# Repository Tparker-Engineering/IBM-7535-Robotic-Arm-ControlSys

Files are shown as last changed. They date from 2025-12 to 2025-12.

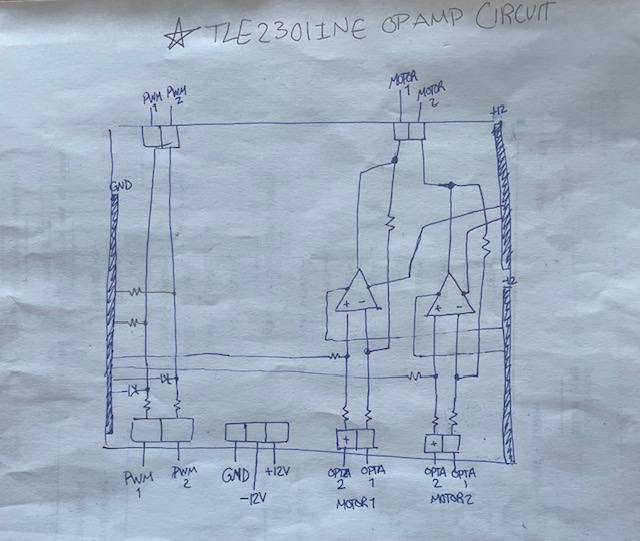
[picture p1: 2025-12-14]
Datasheets_Wiring/OpAmpCircuit.jpg

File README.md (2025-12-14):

# IBM-7535-Robotic-Arm-ControlSys

Watch the demo video (https://youtu.be/oRWTlzxxvLM)

## Project Overview
**Rewired & ReARMed** is a senior design project focused on retrofitting an **IBM 7535 SCARA robot** from the 1980s with modern control hardware and software.  
The goal was to replace the obsolete control system with an **Arduino Opta PLC** while maintaining the robot’s functionality and old legacy systems.

Originally designed for industrial automation, the IBM 7535 had been rendered non-functional due to outdated electronics, limited documentation, and component issues. Our team reverse-engineered the system, traceed its wiring diagrams, and designed a new control approach compatible with the existing **Yaskawa Servopak motor drivers**. This included:
- developing an **analog ±10V control solution** using op-amp subtractor circuits, enabling bidirectional motor control from the Arduino Opta’s 0–10V outputs
- making a **voltage divider circuit using Zener diodes** to enable bidirectional control for the stepper motor
- successfully pulse the stepper motor at operable speed
- send voltage to operate the solenoids

In addition to wiring the OPTA to the system, we programmed control logic within the Arduino IDE, verified the sensors, and ensured the motors responded accurately to control inputs. The result was a functioning robot capable of smooth and controlled movement, demonstrated successfully in a live test.
While the SCARA is operable and functionable, it still needs future work, like finishing the encoders and tracing a possible overcurrent issue in the servopacks, an issue that is correlated to the motor drift.
Despite the small issues, the team was able to pave a way for future teams to work on the 7535 SCARA and hopes to see the robotic arm be completely restored and retrofitted with the versatility and capability of modern technology.

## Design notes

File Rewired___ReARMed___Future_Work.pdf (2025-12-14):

# Rewired & ReARMed - Future Work

AnMinh Vuong | Rachel Garcia | Travis Parker
Xander Addington | Angelina Abuhilal
| July 2025

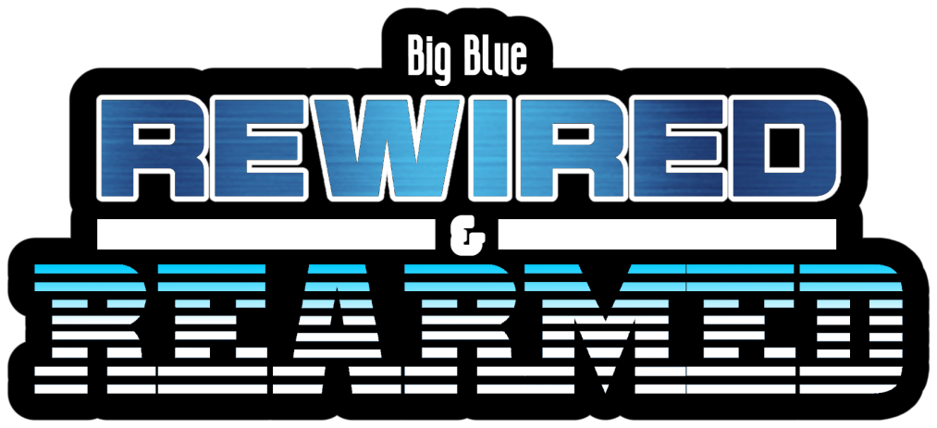
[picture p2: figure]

1

## Introduction

This document is meant for the next team who ends up with the robot. We wanted to be able to share our thoughts and concerns with the project in the future.

## System Startup Notes

- For any test or demo code, position the Theta1 arm slightly clockwise of the home sensor before startup. The Theta2 arm should also be slightly clockwise of the home sensor; the robot will drift counterclockwise into the sensor during initialization.

## Encoder and Sensor Wiring

- Encoders on WD12A are wired to pins 3, 1, and 5. Future teams may need to supply +12 V to pin 19 and GND to pins 2, 4, and 6 (to be verified).
- On WD13A, encoders are wired to pins 7, 9, and 11.
- For Theta1 and Z-axis gripper sensors, a temporary software pull hack was used; a proper pull resistor circuit is recommended.
- Stepper motor sensors (R+ Area and Rhome) on WD08B are currently non-functional; further troubleshooting is required.

## Safety Recommendations

- Implement an emergency shut-off switch between TB1R and ground; TB1R to ground enables power to the manipulator.
- Improve initialization routines and safety logic in software.

## Circuit Limitations and Recommendations

- Current op-amp circuit is limited to 5 V output. Avoid exceeding this due to unknown servo potentiometer settings.
- Recommend creating a proper PCB instead of continuing with prototype boards.

2

## Wiring and Connectors

- Existing wiring with Deutsch connectors was reused. Spare Deutsch pins are provided for future wiring.
- If possible, design improved wiring harnesses and connectors.

## Servo and Encoder Issues

- Encoders may be causing servo drift in Theta1 and Theta2 due to undervoltage (red servo light indicator).
- If encoder fixes do not stop red lights, investigate possible overcurrent, undercurrent, overvoltage, or undervoltage conditions.

## Removed Legacy Hardware

- Removed MTCB, CPU, and FEC boards. The relay board can be removed, but TB1R is attached to it.

## Future Software Goals

- Optical encoders should enable precise position control (e.g., Theta1 = 61, Theta2 = 120 should move directly to that position).
- Develop a touchscreen GUI tablet similar to the original (now obsolete) controller.

## Priorities for Future Teams

Computer Engineering:

1. Get encoders working.
2. Get stepper limit sensors working.
3. Install emergency shut-off switch.
4. Improve circuit design and wiring.
5. Mount Arduino Opta units to DIN rail and robot.

Secondary:
- Troubleshoot servos if encoder fixes fail.

Computer Science and Software:

1. Develop GUI.
2. Assist CpE team with encoder position grid/matrix.

3

## Contacts

AnMinh Vuong
Discord - Zetsubou999
Email - anminh0102@gmail.com

Travis Parker
Discord - dvrkstar

Angie Abuhilal
Discord - farfarahah

Xander Addington
Discord - xer0727

Rachel Garcia
Discord - rig3121

4

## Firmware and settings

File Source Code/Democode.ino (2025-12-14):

#include "OptaBlue.h"

/*Theta1 needs to be slight off home cam roller. Theta2 needs to be slightly off home sensor. Stepper belt needs to be in a safe postion. 
Close air compressor valve on bottom of aircompressor and plug in compressor. PSI for robot is 80PSI do not exceed.
Demo will execute a simulation of pick and place operation.*/

// Relay outputs
#define Z_DOWN_RELAY    0  // RELAY1 (D0)
#define GRIPPER_RELAY   1  // RELAY2 (D1)

// Sensor inputs (core Opta GPIO)
#define Z_UP_PIN        A6  // Z-UP sensor input
#define Z_DOWN_PIN      A2  // Z-DOWN sensor input

bool gripperCycleDone = false;

enum Theta1State {
  THETA1_IDLE,
  THETA1_MOVE_CCW_1,
  THETA1_HOLD_1,
  THETA1_MOVE_CCW_2,
  THETA1_HOLD_2,
  THETA1_TO_OVERRUN,
  THETA1_TO_HOME,
  THETA1_DONE
};

enum Theta2State {
  THETA2_IDLE,
  THETA2_MOVE_CCW_1,
  THETA2_HOLD_1,
  THETA2_MOVE_CCW_2,
  THETA2_HOLD_2,
  THETA2_TO_OVERRUN_POS,
  THETA2_TO_OVERRUN_NEG,
  THETA2_TO_HOME,
  THETA2_DONE
};

Theta1State theta1_state = THETA1_IDLE;
Theta2State theta2_state = THETA2_IDLE;

bool stepper_active = false;
uint32_t stepper_start_time = 0;
uint8_t stepper_channel = 0;


AnalogExpansion aexp;
float lastVoltages[7] = {0};

void safeSetVoltage(uint8_t channel, float voltage) {
  if (lastVoltages[channel] != voltage) {
    aexp.pinVoltage(channel, voltage);
    lastVoltages[channel] = voltage;
  }
}

void spinStepper(uint8_t channel) {
  aexp.setPwm(channel, 1600, 25);
  OptaController.update();
  delay(250);
  aexp.setPwm(channel, 1600, 0);
  OptaController.update();
}
/*
void runGripperSequence() {
  // Z-UP pull-up hack
  pinMode(Z_UP_PIN, OUTPUT); digitalWrite(Z_UP_PIN, HIGH); delay(1);
  pinMode(Z_UP_PIN, INPUT); delayMicroseconds(5);
  bool zUpActive = (digitalRead(Z_UP_PIN) == LOW);

  // === Software pull-up hack for Z-DOWN (A2) ===
  pinMode(Z_DOWN_PIN, OUTPUT);
  digitalWrite(Z_DOWN_PIN, HIGH);
  delay(1);
  pinMode(Z_DOWN_PIN, INPUT);
  delayMicroseconds(5);
  bool zDownActive = (digitalRead(Z_DOWN_PIN) == LOW);  // active-low

  digitalWrite(Z_DOWN_RELAY, HIGH);  // Lower Z
  delay(1000);
  digitalWrite(Z_DOWN_RELAY, LOW);  // Raise Z
  delay(200);

/*
  if (zUpActive) {
    digitalWrite(Z_DOWN_RELAY, HIGH);  // Lower Z
    delay(500);

    unsigned long startTime = millis();
    while ((millis() - startTime) < 5000) {
      // Z-DOWN pull-up hack
      pinMode(Z_DOWN_PIN, OUTPUT); digitalWrite(Z_DOWN_PIN, HIGH); delay(1);
      pinMode(Z_DOWN_PIN, INPUT); delayMicroseconds(5);
      bool zDownActive = (digitalRead(Z_DOWN_PIN) == LOW);

      if (zDownActive) {
        digitalWrite(GRIPPER_RELAY, HIGH);  // Grip
        delay(1000);
        digitalWrite(GRIPPER_RELAY, LOW);
        break;
      }
    }

    digitalWrite(Z_DOWN_RELAY, LOW);  // Raise Z
  }
  
  delay(200);
}
*/

// Timing parameters
const unsigned long theta1_moveDuration1 = 4000;
const unsigned long theta1_moveDuration2 = 2000;
const unsigned long theta1_holdDuration = 4000;
unsigned long theta1_timer = 0;

const unsigned long theta2_moveDuration1 = 1250;
const unsigned long theta2_moveDuration2 = 500;
const unsigned long theta2_holdDuration1 = 8000;
const unsigned long theta2_holdDuration2 = 4000;
unsigned long theta2_timer = 0;

void setup() {
  Serial.begin(115200);
  OptaController.begin();

  pinMode(A0, INPUT_PULLUP);  // θ₁ home
  pinMode(A1, INPUT_PULLUP);  // θ₁ overrun
  pinMode(A3, INPUT_PULLUP);  // θ₂ home
  pinMode(A4, INPUT_PULLUP);  // θ₂ overrun−
  pinMode(A5, INPUT_PULLUP);  // θ₂ overrun+
  // Set relay outputs
  pinMode(Z_DOWN_RELAY, OUTPUT);
  pinMode(GRIPPER_RELAY, OUTPUT);
  digitalWrite(Z_DOWN_RELAY, LOW);
  digitalWrite(GRIPPER_RELAY, LOW);


  while (OptaController.getExpansionNum() == 0) {
    Serial.println("Waiting for analog expansion...");
    OptaController.update();
  }

  aexp = OptaController.getExpansion(0);

  aexp.beginChannelAsDac(2, OA_VOLTAGE_DAC, true, false, OA_SLEW_RATE_0);  // θ₁ CW
  aexp.beginChannelAsDac(3, OA_VOLTAGE_DAC, true, false, OA_SLEW_RATE_0);  // θ₁ CCW
  aexp.beginChannelAsDac(5, OA_VOLTAGE_DAC, true, false, OA_SLEW_RATE_0);  // θ₂ CW
  aexp.beginChannelAsDac(6, OA_VOLTAGE_DAC, true, false, OA_SLEW_RATE_0);  // θ₂ CCW

  aexp.setPwm(OA_PWM_CH_0, 1600, 0);  // Stepper CCW idle
  aexp.setPwm(OA_PWM_CH_1, 1600, 0);  // Stepper CW idle

  safeSetVoltage(2, 0.0f);
  safeSetVoltage(3, 0.4f);
  safeSetVoltage(5, 0.0f);
  safeSetVoltage(6, 0.4f);

  OptaController.update();
  Serial.println("Setup complete.");
}

void loop() {

  // θ₁ sensor reads
  pinMode(A0, OUTPUT); digitalWrite(A0, HIGH); delayMicroseconds(10);
  pinMode(A0, INPUT); delayMicroseconds(5);
  bool theta1_home = (digitalRead(A0) == LOW);

  pinMode(A1, OUTPUT); digitalWrite(A1, HIGH); delayMicroseconds(10);
  pinMode(A1, INPUT); delayMicroseconds(5);
  bool theta1_overrun = (digitalRead(A1) == LOW);

  // θ₂ sensor reads
  bool theta2_home = (digitalRead(A3) == LOW);
  bool theta2_overrunNeg = (digitalRead(A4) == LOW);
  bool theta2_overrunPos = (digitalRead(A5) == LOW);

  bool zDownActive = (digitalRead(Z_DOWN_PIN) == LOW);  // active-low
  bool zUpActive = (digitalRead(Z_UP_PIN) == LOW);


  OptaController.update();

  // θ₁ State Machine
  switch (theta1_state) {
    case THETA1_IDLE:
      safeSetVoltage(2, 0.0f);
      safeSetVoltage(3, 0.4f);
      if (theta1_home) {
        theta1_timer = millis();
        Serial.println("θ₁ → MOVE_CCW_1");
        theta1_state = THETA1_MOVE_CCW_1;
      }
      break;

    case THETA1_MOVE_CCW_1:
      safeSetVoltage(2, 0.0f);
      safeSetVoltage(3, 4.5f);
      if (millis() - theta1_timer >= theta1_moveDuration1) {
        safeSetVoltage(3, 0.0f);
        theta1_timer = millis();
        Serial.println("θ₁ → HOLD_1");
        theta1_state = THETA1_HOLD_1;
      }
      break;

    case THETA1_HOLD_1:
      safeSetVoltage(2, 0.0f);
      safeSetVoltage(3, 0.4f);
        
        aexp.setPwm(OA_PWM_CH_0, 1600, 25);  // start CCW
        OptaController.update();
        delay(250);
        aexp.setPwm(OA_PWM_CH_0, 1600, 1);  // almost 0% duty
        OptaController.update();
        delay(2);                               // allow hardware to register
        aexp.setPwm(OA_PWM_CH_0, 1600, 0);  // now fully stop
        OptaController.update();
        //runGripperSequence();

        delay(400);
        // Z-UP pull-up hack
        pinMode(Z_UP_PIN, OUTPUT); digitalWrite(Z_UP_PIN, HIGH); delay(1);
        pinMode(Z_UP_PIN, INPUT); delayMicroseconds(5);

        // === Software pull-up hack for Z-DOWN (A2) ===
        pinMode(Z_DOWN_PIN, OUTPUT);
        digitalWrite(Z_DOWN_PIN, HIGH);
        delay(1);
        pinMode(Z_DOWN_PIN, INPUT);
        delayMicroseconds(5);


        digitalWrite(Z_DOWN_RELAY, HIGH);  // Lower Z
        delay(1000);
        digitalWrite(Z_DOWN_RELAY, LOW);  // Raise Z
        delay(1000);


        delay(4000);
      /*
      if (stepper_active && millis() - stepper_start_time <= 300) {
        aexp.setPwm(stepper_channel, 1600, 1);  // almost 0% duty
        delay(2);                               // allow hardware to register
        aexp.setPwm(stepper_channel, 1600, 0);  // now fully stop
        OptaController.update();                // apply to hardware
        OptaController.update();
        stepper_active = false;
      }
      
      //spinStepper(OA_PWM_CH_0);  // For CCW
      if (!stepper_active) {
        aexp.setPwm(OA_PWM_CH_0, 1600, 25);  // start CCW
        OptaController.update();
        stepper_channel = OA_PWM_CH_0;
        stepper_start_time = millis();
        stepper_active = true;
        Serial.println("θ₁: Spinning stepper CCW");
      }
      
      */
      // Serial.println("θ₁: Spinning stepper CCW");
      if (millis() - theta1_timer >= theta1_holdDuration) {
        theta1_timer = millis();
        Serial.println("θ₁ → MOVE_CCW_2");
        theta1_state = THETA1_MOVE_CCW_2;
      }
      break;

    case THETA1_MOVE_CCW_2:
      safeSetVoltage(2, 0.0f);
      safeSetVoltage(3, 4.5f);
      if (millis() - theta1_timer >= theta1_moveDuration2) {
        safeSetVoltage(3, 0.0f);
        theta1_timer = millis();
        Serial.println("θ₁ → HOLD_2");
        theta1_state = THETA1_HOLD_2;
      }
      break;

    case THETA1_HOLD_2:
      safeSetVoltage(2, 0.0f);
      safeSetVoltage(3, 0.4f);
      // spinStepper(OA_PWM_CH_1);  // For CW

      delay(400);
      // Z-UP pull-up hack
      if (!gripperCycleDone) {
        delay(400);

        // Pull-up hack for Z-UP
        pinMode(Z_UP_PIN, OUTPUT); digitalWrite(Z_UP_PIN, HIGH); delay(1);
        pinMode(Z_UP_PIN, INPUT); delayMicroseconds(5);

        // Pull-up hack for Z-DOWN
        pinMode(Z_DOWN_PIN, OUTPUT);
        digitalWrite(Z_DOWN_PIN, HIGH);
        delay(1);
        pinMode(Z_DOWN_PIN, INPUT);
        delayMicroseconds(5);

        Serial.println("Z lowering...");
        digitalWrite(Z_DOWN_RELAY, HIGH);
        delay(1000);
        Serial.println("Z raising...");
        digitalWrite(Z_DOWN_RELAY, LOW);
        delay(1000);

        gripperCycleDone = true;
      }


      //runGripperSequence();

        /*
        aexp.setPwm(OA_PWM_CH_1, 1600, 25);  // start CCW
        OptaController.update();
        delay(250);
        aexp.setPwm(OA_PWM_CH_1, 1600, 1);  // almost 0% duty
        OptaController.update();
        delay(2);                               // allow hardware to register
        aexp.setPwm(OA_PWM_CH_1, 1600, 0);  // now fully stop
        OptaController.update();
        */

      /*
      if (!stepper_active) {
        aexp.setPwm(OA_PWM_CH_1, 1600, 25);  // start CCW
        OptaController.update();
        stepper_channel = OA_PWM_CH_0;
        stepper_start_time = millis();
        stepper_active = true;
        Serial.println("θ₁: Spinning stepper CCW");
      }
      */

      if (millis() - theta1_timer >= theta1_holdDuration) {
        Serial.println("θ₁: Spinning stepper CW");
        Serial.println("θ₁ → TO_OVERRUN");
        safeSetVoltage(3, 4.5f);

        theta1_state = THETA1_TO_OVERRUN;
      }
      break;

    case THETA1_TO_OVERRUN:
      if (theta1_overrun) {
        Serial.println("θ₁ overrun detected. Returning home.");
        safeSetVoltage(2, 5.2f);
        safeSetVoltage(3, 0.0f);
        theta1_state = THETA1_TO_HOME;
      }
      break;

    case THETA1_TO_HOME:
      if (theta1_home) {
        Serial.println("θ₁ returned to home.");
        safeSetVoltage(2, 0.0f);
        safeSetVoltage(3, 0.0f);
        theta1_state = THETA1_DONE;
      }
      break;

    case THETA1_DONE:
      // No action
      break;
  }

  // θ₂ State Machine
  switch (theta2_state) {
    case THETA2_IDLE:
      safeSetVoltage(5, 0.0f);
      safeSetVoltage(6, 0.4f);
      if (theta2_home) {
        theta2_timer = millis();
        Serial.println("θ₂ → MOVE_CCW_1");
        theta2_state = THETA2_MOVE_CCW_1;
      }
      break;

    case THETA2_MOVE_CCW_1:
      safeSetVoltage(5, 0.0f);
      safeSetVoltage(6, 4.5f);
      if (millis() - theta2_timer >= theta2_moveDuration1) {
        safeSetVoltage(6, 0.0f);
        theta2_timer = millis();
        Serial.println("θ₂ → HOLD_1");
        theta2_state = THETA2_HOLD_1;
      }
      break;

    case THETA2_HOLD_1:
      safeSetVoltage(5, 0.0f);
      safeSetVoltage(6, 0.4f);
      if (millis() - theta2_timer >= theta2_holdDuration1) {
        theta2_timer = millis();
        Serial.println("θ₂ → MOVE_CCW_2");
        theta2_state = THETA2_MOVE_CCW_2;
      }
      break;

    case THETA2_MOVE_CCW_2:
      safeSetVoltage(5, 0.0f);
      safeSetVoltage(6, 4.5f);
      if (millis() - theta2_timer >= theta2_moveDuration2) {
        safeSetVoltage(6, 0.0f);
        theta2_timer = millis();
        Serial.println("θ₂ → HOLD_2");
        theta2_state = THETA2_HOLD_2;
      }
      break;

    case THETA2_HOLD_2:
      safeSetVoltage(5, 0.0f);
      safeSetVoltage(6, 0.4f);
      if (millis() - theta2_timer >= theta2_holdDuration2) {
        Serial.println("θ₂ → TO_OVERRUN_POS");
        safeSetVoltage(6, 4.5f);
        theta2_state = THETA2_TO_OVERRUN_POS;
      }
      break;

    case THETA2_TO_OVERRUN_POS:
      if (theta2_overrunPos) {
        Serial.println("θ₂ → TO_OVERRUN_NEG");
        safeSetVoltage(5, 5.2f);
        safeSetVoltage(6, 0.0f);
        theta2_state = THETA2_TO_OVERRUN_NEG;
      }
      break;

    case THETA2_TO_OVERRUN_NEG:
      if (theta2_overrunNeg) {
        Serial.println("θ₂ → TO_HOME");
        safeSetVoltage(5, 0.0f);
        safeSetVoltage(6, 4.5f);
        theta2_state = THETA2_TO_HOME;
      }
      break;

    case THETA2_TO_HOME:
      if (theta2_home) {
        Serial.println("θ₂ returned to home.");
        safeSetVoltage(5, 0.0f);
        safeSetVoltage(6, 0.0f);
        theta2_state = THETA2_DONE;
      }
      break;

    case THETA2_DONE:
      // No action
      break;
  }

  delay(20);
}

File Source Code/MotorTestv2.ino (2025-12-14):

#include "OptaBlue.h"

bool testDone = false;

void setup() {
  Serial.begin(115200);
  delay(1000);

  OptaController.begin();

  // Wait until the analog expansion is detected
  while (OptaController.getExpansionNum() == 0) {
    Serial.println("Waiting for expansion...");
    OptaController.update();
    delay(500);
  }

  // Get the expansion object
  AnalogExpansion exp = OptaController.getExpansion(0);

  if (exp) {
    // Correct usage: non-static method, 5 arguments
    exp.beginChannelAsDac(5, OA_VOLTAGE_DAC, true, false, OA_SLEW_RATE_0);  // I5
    exp.beginChannelAsDac(6, OA_VOLTAGE_DAC, true, false, OA_SLEW_RATE_0);  // I6
    delay(1000);  // Let DAC stabilize
  }
}

void loop() {
  AnalogExpansion exp = OptaController.getExpansion(0);

  if (!testDone && exp) {
    Serial.println("Motor 2 -2.5V");
    exp.pinVoltage(5, 4.6f, true);
    exp.pinVoltage(6, 0.0f, true);
    delay(2000);

    Serial.println("Motor 2 -5V");
    exp.pinVoltage(5, 8.1f, true);
    exp.pinVoltage(6, 0.0f, true);
    delay(2000);

    Serial.println("Motor 2 2.5V");
    exp.pinVoltage(5, 0.0f, true);
    exp.pinVoltage(6, 5.2f, true);
    delay(2000);

    Serial.println("Motor 2 5V");
    exp.pinVoltage(5, 0.0f, true);
    exp.pinVoltage(6, 8.6f, true);
    delay(2000);

    testDone = true;
  }

  OptaController.update();
}

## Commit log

2025-12-14 OpAmp and voltage divider layout
2025-12-14 OpAmp, voltage divider and integrated wiring
    [IBM7535OPTATB1RBypass.kicad_sch, IBM7535OPTATHETA1-THETA2-ENCO-STEPPERR-AREAR-HOME.kicad_sch, IBM7535OPTATHETA1THETA2.kicad_sch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]
2025-12-15 Gripper and Air test with position detection.
2025-12-15 Motor test code
2025-12-15 Operates stepper motor and stop.
2025-12-15 Exercises the Theta1 motor with use of the sensor.
2025-12-15 Theta2 Test with sensor detection
